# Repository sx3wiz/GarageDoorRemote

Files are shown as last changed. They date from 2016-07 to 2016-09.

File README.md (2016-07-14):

# GarageDoorRemote

This project is an OSHW garage door keychain remote and receiver. This project is not garage door opener brand specific. It takes advantage of the fact that almost all garage dooor openers have a NO contact input to trigger a opening/closing cycle.

## Project Goals

1. Small remote form factor
 * Keychain sized
2. Long battery life on remote
3. High security
 * No replay attacks
 * Secure encryption during pairing
3. Decent range
 * About 25 meters

## Directory Structure
* hardware/
 * Contains all OSHW designs for the remote and receiver
* software/
 * Contains all software for remote and receiver

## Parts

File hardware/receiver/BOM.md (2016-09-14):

# Bill of materials

### Version vX.X

Componet Refs  | Type            | Value       | Package  | Qty | Digikey Part #
---------------|-----------------|-------------|----------|-----|---------------
U1             | microcontroller | n/a         | 32-TQFP  | 1   | ATMEGA328P-AU-ND
U2             | transceiver     | 433mhz      | 16-smd   | 1   | 1568-1391-ND
U3             | linear regulator| 3.3v/100ma  | SOIC-8   | 1   | 497-6880-1-ND
R1, R2         | resistor        | 10k         | 0603     | 2   | 311-10.0KLRCT-ND
R3             | resistor        | 47k         | 0603     | 1   | P47KJCT-ND
C1             | capacitor       | 10uF/6.3V   | 0603     | 1   | 490-3896-1-ND
C2, C3         | capacitor       | 100nF/16V   | 0603     | 2   | 490-3261-1-ND
Q1             | n-ch mosfet     | Id=4.3A     | SOT-23-3 | 1   | BSS214N H6327CT-ND
D1, D2         | diode           | Io=1A       | SOD-323  | 2   | SBR130S3-7DICT-ND
U4             | relay           | SPST        | SIP-4    | 1   | 306-1062-ND
J2             | barrel jack     | n/a         | 5.5x2.1mm| 1   | (Sparkfun) PRT-10811
J1             | screw terminal  | n/a         | 1x2 5mm  | 1   | n/p
J3             | male header     | n/a         | 6x2 0.1" | 1   | n/p
J4             | male header     | n/a         | 1x2 0.1" | 1   | n/p
J5             | male header     | n/a         | 1x10 0.1"| 1   | n/p

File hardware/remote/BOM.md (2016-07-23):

# Bill of materials

### Version vX.X

Componet Refs  | Type            | Value       | Package  | Qty | Digikey Part #
---------------|-----------------|-------------|----------|-----|---------------
U1             | microcontroller | n/a         | 28-VQFN  | 1   | ATMEGA328P-MMH-ND
U2             | transceiver     | 433mhz      | 16-smd   | 1   | 1568-1391-ND
R1             | resistor        | 10k         | 0603     | 1   | 311-10.0KLRCT-ND
R2             | resistor        | 47k         | 0603     | 1   | P47KJCT-ND
C1, C2         | capacitor       | 100nF/16V   | 0603     | 2   | 490-3261-1-ND
C3             | capacitor       | 10uF/6.3V   | 0603     | 1   | 490-3896-1-ND
S1             | switch          | Mom. NO     | 4-pth    | 1   | (Sparkfun) COM-00097
BAT1           | battery holder  | 20mm        | 4-smd    | 1   | (Sparkfun) PRT-11892
J1             | male header     | n/a         | 6x2 0.1" | 1   | n/a

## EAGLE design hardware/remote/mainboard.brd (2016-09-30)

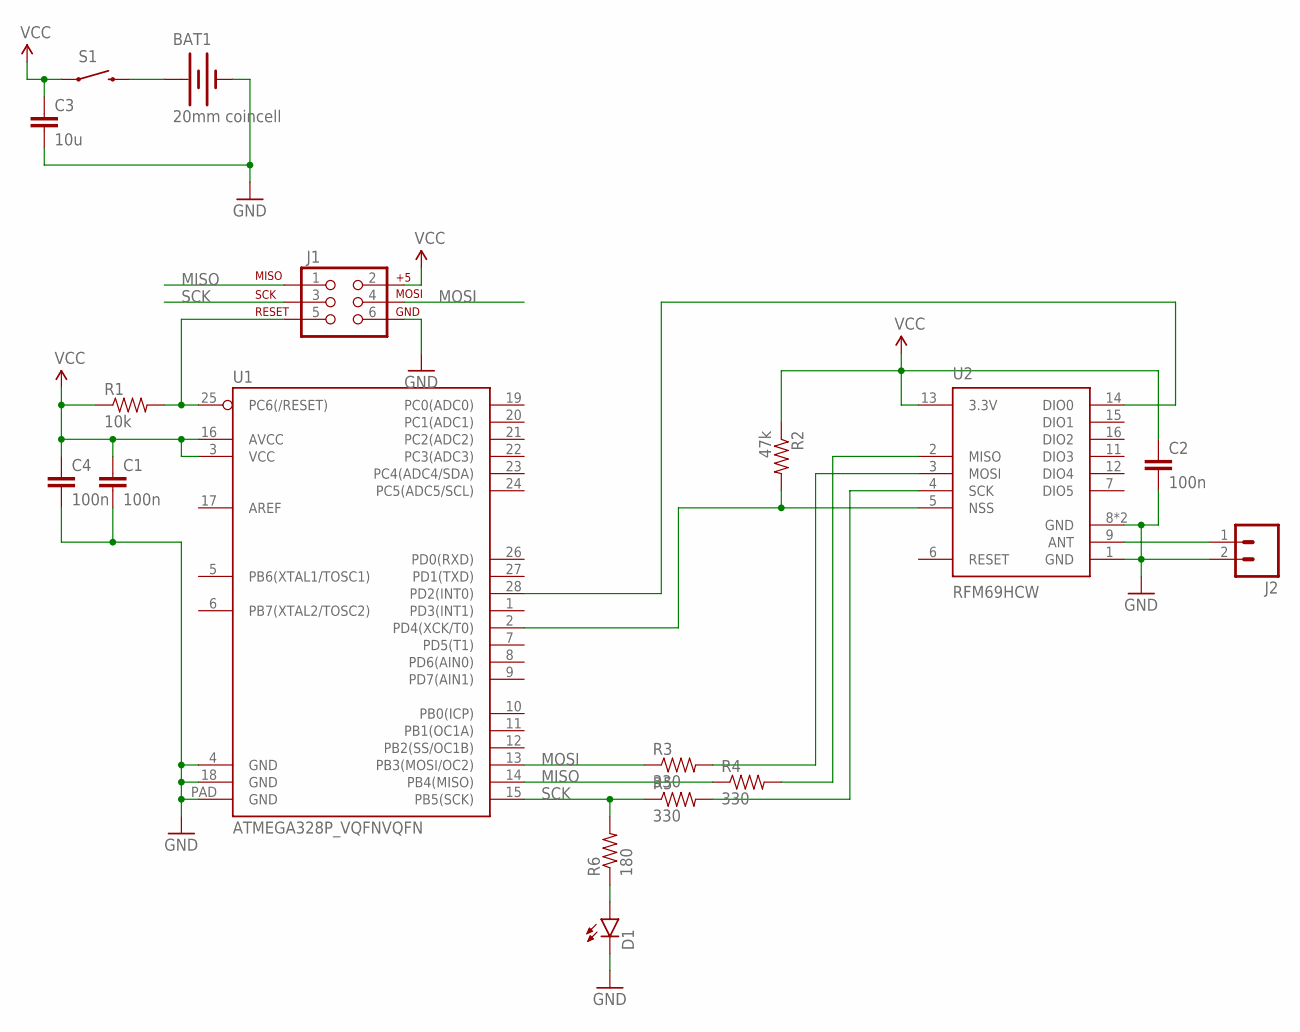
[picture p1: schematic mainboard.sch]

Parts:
BAT1: 20mm coincell; BATTCON_20MM_4LEGS
C1, C2, C4: 100n; 0603-CAP
C3: 10u; 1206
D1: LED0603; LED-0603
J1: AVR_SPI_PRG_6PTH; 2X3
J2: M02PTH; 1X02
R1: 10k; 0603-RES
R2: 47k; 0603-RES
R3, R4, R5: 330; 0603-RES
R6: 180; 0603-RES
S1: SWITCH-MOMENTARY-2PTH; TACTILE-PTH
U1: ATMEGA328P_VQFNVQFN; VQFN-28
U2: RFM69HCW; RFM69HCW-XXXS2

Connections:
GND: BAT1.NEGATIVE (-), C1.2, C2.2, C3.2, C4.2, D1.C, J1.6, J2.2, U1.4 (GND), U1.18 (GND), U1.PAD (GND), U2.1 (GND), U2.8 (GND), U2.10 (GND)
MISO: J1.1, R4.1, U1.14 (PB4(MISO))
MOSI: J1.4, R3.1, U1.13 (PB3(MOSI/OC2))
unnamed: BAT1.POSITIVE@1 (+), BAT1.POSITIVE@2 (+), BAT1.POSITIVE@3 (+), BAT1.POSITIVE@4 (+), S1.3 (2)
unnamed: J1.5, R1.2, U1.25 (PC6(/RESET))
unnamed: R3.2, U2.3 (MOSI)
unnamed: J2.1, U2.9 (ANT)
unnamed: R4.2, U2.2 (MISO)
unnamed: R2.2, U1.2 (PD4(XCK/T0)), U2.5 (NSS)
unnamed: R5.2, U2.4 (SCK)
unnamed: U1.28 (PD2(INT0)), U2.14 (DIO0)
unnamed: D1.A, R6.1
SCK: J1.3, R5.1, R6.2, U1.15 (PB5(SCK))
VCC: C1.1, C2.1, C3.1, C4.1, J1.2, R1.1, R2.1, S1.1, U1.3 (VCC), U1.16 (AVCC), U2.13 (3.3V)

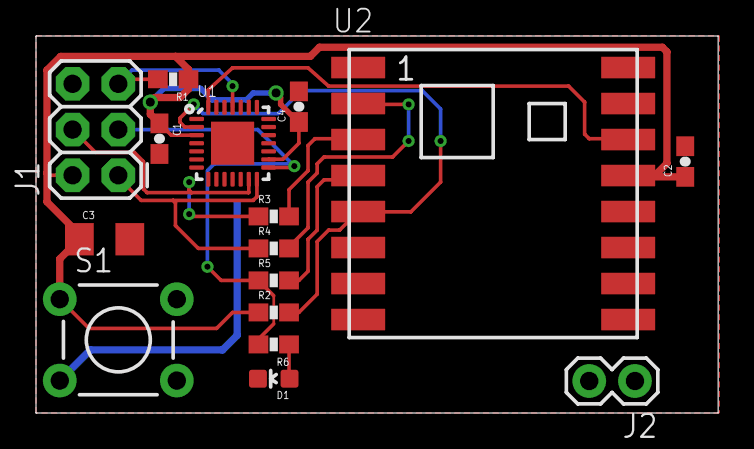
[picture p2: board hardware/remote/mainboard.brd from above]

Board: 2 copper layers, 37.9 x 20.9 mm, 17 parts (1 on the bottom side), 14 nets.

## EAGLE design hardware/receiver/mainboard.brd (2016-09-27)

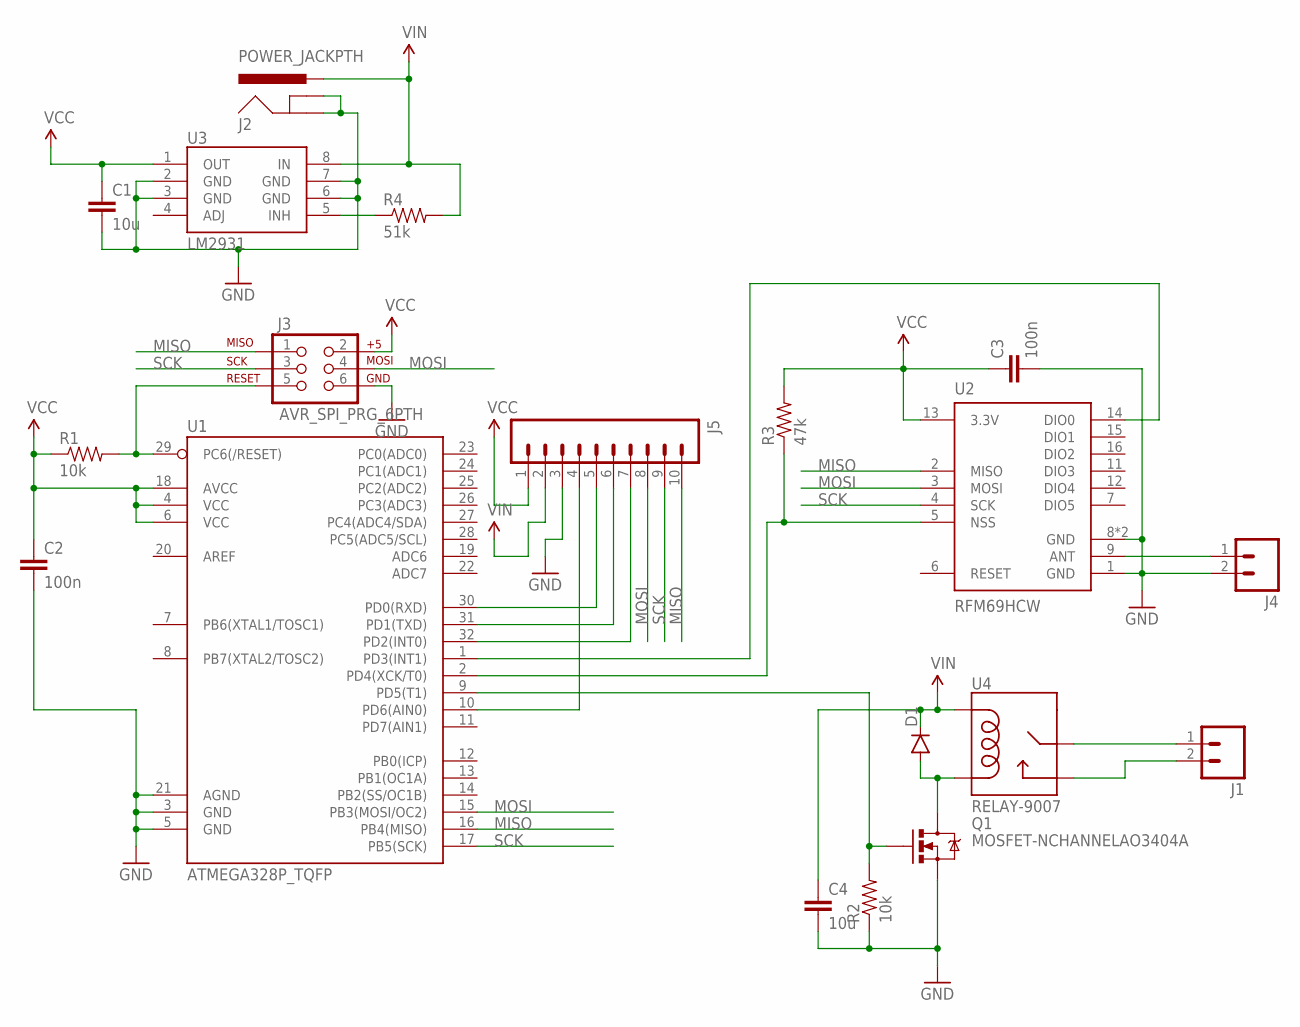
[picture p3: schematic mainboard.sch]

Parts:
C1, C4: 10u; 1206
C2, C3: 100n; 0603-CAP
D1: DIODEBAS16; SOD-323
J1: M025MM; SCREWTERMINAL-5MM-2
J2: POWER_JACKPTH; POWER_JACK_PTH
J3: AVR_SPI_PRG_6PTH; 2X3
J4: M02PTH; 1X02
J5: M10SILK_FEMALE_PTH; 1X10
Q1: MOSFET-NCHANNELAO3404A; SOT23-3
R1, R2: 10k; 0603-RES
R3: 47k; 0603-RES
R4: 51k; 0603-RES
U1: ATMEGA328P_TQFP; TQFP32-08
U2: RFM69HCW; RFM69HCW-XXXS2
U3: LM2931; SO08
U4: RELAY-9007

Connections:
GND: C1.2, C2.2, C3.2, C4.2, J2.GND, J2.GNDBREAK, J3.6, J4.2, J5.3, Q1.2 (S), R2.1, U1.3 (GND), U1.5 (GND), U1.21 (AGND), U2.1 (GND), U2.8 (GND), U2.10 (GND), U3.2 (GND), U3.3 (GND), U3.6 (GND), U3.7 (GND)
MISO: J3.1, J5.10, U1.16 (PB4(MISO)), U2.2 (MISO)
MOSI: J3.4, J5.8, U1.15 (PB3(MOSI/OC2)), U2.3 (MOSI)
unnamed: R3.1, U1.2 (PD4(XCK/T0)), U2.5 (NSS)
unnamed: J3.5, R1.2, U1.29 (PC6(/RESET))
unnamed: U1.1 (PD3(INT1)), U2.14 (DIO0)
unnamed: J4.1, U2.9 (ANT)
unnamed: J1.1, U4.1 (MAIN)
unnamed: J1.2, U4.4 (NO)
unnamed: D1.A, Q1.3 (D), U4.3 (COIL2)
unnamed: Q1.1 (G), R2.2, U1.9 (PD5(T1))
unnamed: J5.7, U1.32 (PD2(INT0))
unnamed: J5.6, U1.31 (PD1(TXD))
unnamed: J5.5, U1.30 (PD0(RXD))
unnamed: J5.4, U1.10 (PD6(AIN0))
unnamed: R4.1, U3.5 (INH)
SCK: J3.3, J5.9, U1.17 (PB5(SCK)), U2.4 (SCK)
VCC: C1.1, C2.1, C3.1, J3.2, J5.1, R1.1, R3.2, U1.4 (VCC), U1.6 (VCC), U1.18 (AVCC), U2.13 (3.3V), U3.1 (OUT)
VIN: C4.1, D1.C, J2.PWR, J5.2, R4.2, U3.8 (IN), U4.2 (COIL1)

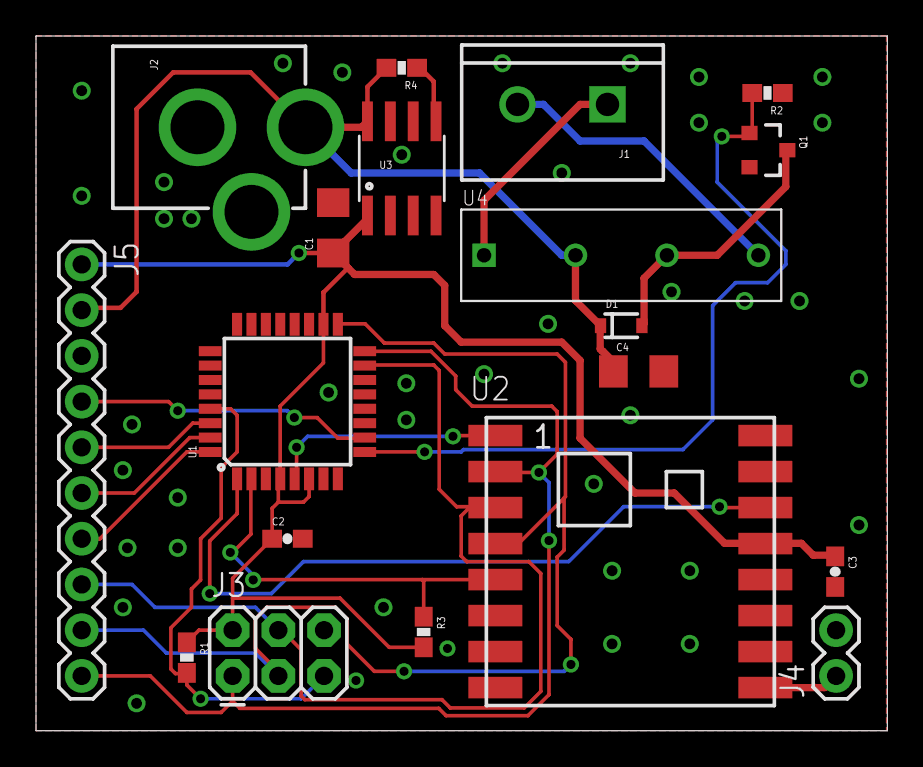
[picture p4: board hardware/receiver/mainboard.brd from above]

Board: 2 copper layers, 47.3 x 38.6 mm, 19 parts (0 on the bottom side), 19 nets.

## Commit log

2016-07-16 Added parts to schematic
    [mainboard.sch]
2016-07-16 Scehamtic work
    [mainboard.sch]
2016-07-16 Preliminary schematic design
    [mainboard.sch]
2016-07-16 PCB component placement and antenna connector
    [mainboard.brd, mainboard.sch]
2016-07-16 Preliminary PCB design
    [mainboard.brd, mainboard.sch]
2016-07-16 Added components to receiver schematic
    [mainboard.sch]
2016-07-17 Preliminary schematic
    [mainboard.sch]
2016-07-17 Added expansion connector
    [mainboard.sch]
2016-07-17 Initial PCB layout
    * Optimized expansion connector for PCB layout
    * Added protection diode to relay
    [mainboard.brd, mainboard.sch]
2016-07-23 Added BOM and modified resistor value
    Remote
    * Added detailed BOM with digikey part numbers.
    * Changed R2 from 50k to 47k as 47k is a much more common value.
    [mainboard.brd, mainboard.sch]
2016-07-23 Added BOM and diode protection
    Receiver
    * Added BOM
    * Issue with relay activation voltage
    * Had to change VIN to 5V and add a regulator to 3.3B
    * Added VIN pin to expansion header
    [mainboard.brd, mainboard.sch]
2016-07-23 Initial PCB layout of Receiver
    * Changed expansion connector pinout to make layout easier
    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
    [mainboard.brd, mainboard.sch]
2016-07-23 Fixed wrong MCU in BOM for receiver
2016-07-23 Fixed SPI mismatch
    [mainboard.brd, mainboard.sch]
2016-09-13 Replaced relay and voltage regulator in schematic
    [mainboard.brd, mainboard.sch]
2016-09-14 Replaced LDO and relay and updated BOM
    [mainboard.brd, mainboard.sch]
2016-09-14 Added ground plane vias
    [mainboard.brd]
2016-09-27 Added frames
    [mainboard.brd, mainboard.sch]
2016-09-30 Added SPI series impedance and status LED
    [mainboard.brd, mainboard.sch]

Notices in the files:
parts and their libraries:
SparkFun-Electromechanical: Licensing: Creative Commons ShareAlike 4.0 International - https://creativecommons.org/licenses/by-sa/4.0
